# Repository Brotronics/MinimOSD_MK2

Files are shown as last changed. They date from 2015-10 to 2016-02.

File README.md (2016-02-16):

# MinimOSD_MK2
MinimOSD made smaller with better pinout and USB.
<br />This work is licensed under a <a rel="license" href="http://creativecommons.org/licenses/by-nc-sa/4.0/">Creative Commons Attribution-NonCommercial-ShareAlike 4.0 International License</a>.

## Firmware

After assembly, review the [Firmware](Firmware.md) notes for loading software.

## Configuration

There are four jumpers that are useful for configuration.

Two are sets of three pads labeled `12-5`.  The one closest to the
`IN` pad sets the camera voltage.  Shorting the two pads on the `12`
side sends 12V to the camera, and the two closest to the `5` side
sends 5V to the camera.  The one nearest the `OUT` pad is the same for
the VTX.

On the same side, there's an `GND` jumper which configures a common
ground for the OSD itself and the video.

On the other side, there's one labeled `+V` which jumps the 5V input
pins so you can have a single 5V input that is used for both outputs
and operating the OSD itself.

## BOM

* [D1, D2, D3 - 3x 0603 LED](http://www.digikey.com/product-detail/en/APT1608SGC/754-1121-1-ND/1747838)
* [D5 - 0805 Schottky](http://www.digikey.com/product-detail/en/SD0805S040S0R5/478-7802-1-ND/3749494)
* [IC4 - MAX7456EUI+](http://www.aliexpress.com/item/5pcs-lot-MAX7456EUI-MAX7456-TSSOP-28-100-NEW-Free-Shipping/32379979937.html)
* [U1 - Atmega 328P AU](http://www.digikey.com/product-detail/en/0/ATMEGA328P-AU-ND)
* [U2 - 0603 1k Resistor Array](http://www.mouser.com/Search/ProductDetail.aspx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) OR [digikey](http://www.digikey.com/product-detail/en/CRA06S0831K00FTA/CRA6S81.00KACT-ND/2665710)
* [U9 - CP2102](http://www.digikey.com/product-detail/en/0/336-1160-1-ND)
* [C1, C2, C3, C4, C5, C6, C17, C19 - 0603 0.1μF](http://www.digikey.com/product-detail/en/0/490-1532-1-ND/587771)
* [R1, R14 - 0603 10kΩ](http://www.digikey.com/product-detail/en/0/RMCF0603FT10K0CT-ND)
* [Y1 - 16MHz resonator](http://www.digikey.com/product-detail/en/PRQC16.00SR5010X000/478-5420-1-ND/1987419)
* [R2, R3 - 0603 75Ω](http://www.digikey.com/product-detail/en/RMCF0603FT75R0/RMCF0603FT75R0CT-ND/1942961)
* [C18 - 1μF cap](http://www.digikey.com/product-detail/en/0/1276-1946-1-ND)
* [Q1 - 27MHz resonator](http://www.mouser.com/Search/ProductDetail.aspx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) OR [digikey](http://www.digikey.com/product-detail/en/XRCGB27M000FAN00R0/490-12140-1-ND/5403022)
* [C7, C8 - 0603 47μF tantalum cap](http://www.digikey.com/product-detail/en/0/478-8644-1-ND/4005804)
* [J1 - USB micro B](http://www.mouser.com/ProductDetail/Molex/47346-0001/?qs=/ha2pyFaduhPJYReNyhO50y8HO7Ogi%252bBiMiNIuS56C8=) or [digikey](http://www.digikey.com/product-detail/en/0473460001/WM17141CT-ND/1782474)

## Board

Top

Bottom

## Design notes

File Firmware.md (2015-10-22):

# [MinimOSD\_MK2](README.md) – Firmware

After assembling the board, the ATMega328p is probably blank from the factory.

The goal is to load the [MW\_OSD](http://www.mwosd.com) Arduino sketch into the device.

First the bootloader, then the sketch.

## Bootloader

The [standard Arduino bootloader for the ATMega328p](https://github.com/arduino/Arduino/blob/master/hardware/arduino/avr/bootloaders/atmega/ATmegaBOOT_168_atmega328.hex) is all that's required. Download it to your PC.

### ISP via Socket Tool

#### AVR ISP Programmer

Firstly you need an ISP Programmer that will bridge the firmware tools on your PC, with the MCU pins used for programming.

While this one is not cheap, it works well and is easily sourced: [Pocket AVR Programmer](https://www.sparkfun.com/products/9825) or [Amazon](http://www.amazon.com/gp/product/B004G54E9I?psc=1&redirect=true&ref_=od_aui_detailpages01)

It's convenient to use a USB extension cable, but either way plug it into your PC.

#### ATMega Socket Tool

This board is too small to take up space with ISP header pads or pins, so using a kind of socket tool that presses down on the pin shoulders will be required.

Hobby King sells the socket tool: [Atmel Atmega Socket Firmware Flashing Tool](https://www.hobbyking.com/hobbyking/store/uh_viewItem.asp?idProduct=27195)

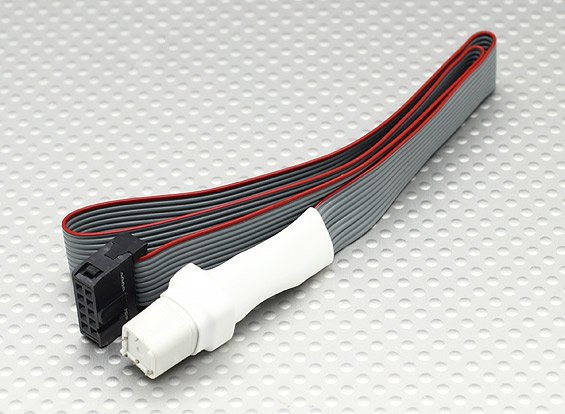
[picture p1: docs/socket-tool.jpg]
socket tool


Plug it in to the AVR ISP Programmer, making sure the pin aligment matches. Normally this is an orientation notch in the header, but it might only be the red strand of the ribbon cable.

#### Host Software

Your PC needs to control the ISP Programmer, and the swiss army knife of host software is `avrdude`.

On Mac OS X, an easy way to install it is to start with [Homebrew](http://brew.sh) and `$ brew install avrdude`.

### Fuses

First set the fuses:

Align the mark on the socket tool with the corner of pin 1 of the ATMega328p and press down evenly.

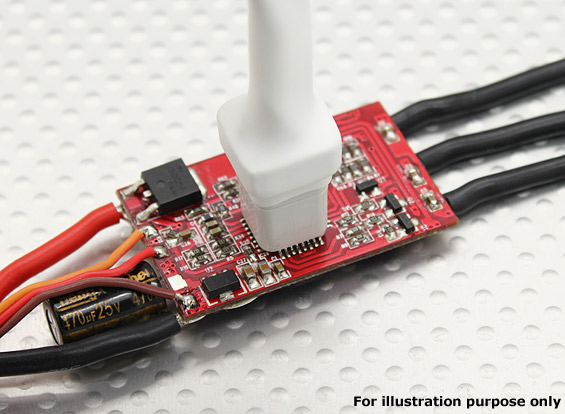
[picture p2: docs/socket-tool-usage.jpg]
socket tool usage


You should see the power light on the OSD illuminate; If not, double check the orientation of the socket tool.

Now issue this avrdude command to set the fuses:

    $ avrdude -c usbtiny -p atmega328p -v -e -U efuse:w:0x05:m -U hfuse:w:0xDA:m -U lfuse:w:0xFF:m

The console output should look something like this at the end:

    avrdude: safemode: lfuse reads as FF
    avrdude: safemode: hfuse reads as DA
    avrdude: safemode: efuse reads as 5
    avrdude: safemode: Fuses OK (E:05, H:DA, L:FF)
    
    avrdude done.  Thank you.

#### Bootloader

Now send the bootloader hex file to the MCU:

    $ avrdude -c usbtiny -p atmega328p -v -e -U efuse:w:0x05:m -U flash:w:ATmegaBOOT_168_atmega328.hex

And verify on the console that the write and verify was successfull:

    avrdude: input file ATmegaBOOT_168_atmega328.hex auto detected as Intel Hex
    avrdude: writing flash (32670 bytes):
    
    Writing | ################################################## | 100% 0.00s
    
    avrdude: 32670 bytes of flash written
    
    ...
    
    avrdude: verifying ...
    avrdude: 32670 bytes of flash verified

Now, remove the socket tool from the MCU; Power light turns off, and you're ready for USB connection.

## MW_OSD

Disconnect the AVR ISP Programmer from your PC.

Plug in a known-working Micro USB cable; You should see your power light illuminate again.

Now launch the [Arduino IDE](https://www.arduino.cc/en/Main/Software) and open the `MW_OSD.ino` file from the [MW\_OSD](http://www.mwosd.com) project.

Configure Arduino IDE

* "Tools" > "Board" > "Arduino Pro or Pro Mini"
* "Tools" > "Processor" > "ATMega328 (5V, 16MHz)"
* "Tools" > "Port" > "/dev/cu.SLAB\_USBtoUART"

_(On a Windows PC, you will need to choose the COM port of the CP2102 driver instead of "/dev/cu.SLAB\_USBtoUART".)_

Edit the `Config.h` file to match your aircraft. At the very least, make sure you choose the "CONTROLLER SOFTWARE" that you intend to use.

Now do "Sketch" > "Upload" to compile, build and upload the MW_OSD firmware to the OSD.

## MW\_OSD\_GUI

Remove the USB cable, and re-connect it to power-cycle the OSD.

Launch the MW\_OSD\_GUI application. Choose the same COM port as above, (or SLAB\_USBtoUART on Mac OS X) and the GUI app will attempt to communicate with the OSD.

A successful connection will show the "MSP:" command codes updating in the far-right column of the GUI app.

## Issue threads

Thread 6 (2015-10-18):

BOM: What part should be used for the Micro USB connector?

ohhorob, 2015-10-18:
I tried transplanting one from a Brotronics PowerTower board, but I probably didn't get it seated properly on the MinimOSD_MK2 (serial port does not show when connecting to a PC; but power light does turn on).

I'll update the BOM if I can get a part that works!

Closed 2015-10-22.

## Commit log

2015-07-08 Initial commit, works.
    [MinimOSD_MK2.GBL, MinimOSD_MK2.GBO, MinimOSD_MK2.GBS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]
2015-09-15 Added a BOM
2015-09-30 BOM Fixes
    - add digikey for resistor array
    - fix digikey link for 16MHz resonator
    - change R2, R3 to 75 ohm; update digikey link too
2015-10-04 Label LEDs in diagram
2015-10-18 BOM Fixe for J1
